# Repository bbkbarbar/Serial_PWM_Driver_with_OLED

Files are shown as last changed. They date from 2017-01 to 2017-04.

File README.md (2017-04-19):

# Serial PWM Driver with optional OLED display

##### Firmware version: 1.5
##### Hardware version: 1.45

#### Table of content:
- [Requirements](#Requirements)
  - [Used MCU](#Device)
  - [Number of output channels](#output_channels)
- [Optional feautres](#Optional_feautres)
  - [Display can be used](#Display_can_be_used)
  - [Handling further channels](#further_channels)
- [Required input line over serial communication](#Required_input_line)
- [Testing, prototyping](#testing_protoryping)
  - [Serial connection (with a Raspberry Pi Zero)](#serial_communitation_with_pi)
  - [Breadboard testing](#Breadboard_testing)
  - [Breadboard testing with all parts on output side](#Breadboard_testing_with_outputs)
- [PCB design](#PCB_design)
  - [Part list](#part_list)
  - [PCB prototype](#PCB_prototype)
  - [First prototype dry test](#prototype_dry_test)
  - [Final placing](#final_placing)
- [Measurements](#Measurements)
  - [Power consumption](#power_consumption)
  - [Memory and program storage utilization on ATmega328](#memory_useage)
- [ToDo list](#todo)
- [Changelog](#changelog)

## <a name="Requirements"> Requirements </a>

 - This device can control individual PWM outputs as "channels".

 - It get commands from any other device over serial communication.

 (e.g.: from a Raspberry Pi or a Bluetooth Serial module)

 - It need to be able to control any DC device at least with 5A power consumption per channel.

 - Need to elecrically separete output channels from MCU circuit and from connected serial device to protect own board and the attached device on the other side of serial communication
 in case of any electrial issue.
 (This will separation is that what will be named as "MCU-side" and "output-side" of this board.)
 This separation based on optocouplers.

 - More output channels need to be able to updated in same time
even if any of those channels has no new value (e.g. When it drives RGB lights and new commands contains only the red and green values)

##### <a name="Device"> Used MCU: </a>
Arduino Nano v3 [(eBay link)](http://www.ebay.com/itm/191773759569?_trksid=p2057872.m2749.l2649&ssPageName=STRK%3AMEBIDX%3AIT)

##### <a name="output_channels"> Number of output channels: </a>
6 channels with 8 bit PWM outputs - based on physical limitation of arduino board.

    Note: Can handle 12bit inputs too.
    For this function define macro:

        USE_12BIT_INPUT_VALUES

### <a name="Optional_feautres"> Optional feautres: </a>

###### <a name="Display_can_be_used"> Display can be used </a> (required library: [Arduino-SSD1306 Ascii](https://github.com/bbkbarbar/Arduino-SSD1306Ascii) ):
    Can handle simple oled display over I2C or SoftSPI protocols to show current values.
    For this feature define one of the following macros:

        USE_OLED_DISPLAY_I2C or
        USE_OLED_DISPLAY_SPI

    Important note:
        Do not define any "USE_OLED_DISPLAY..." macro (comment it out) if display is not connected.
        It will stop working when it tries to communicate with the display and there is no display.

###### <a name="further_channels"> Handling further channels </a>

    Can handle more than 6 channels (what is the physical limitation
    by number of pwm channels on Arduino Nano board)
    If this feature is in use, then it forwards the received commands for a "slave instance"
    when the channel id (of the received command) is over the range of "own channels".
    A second, SoftwareSerial bus is used for forwarding of command to the slave instance of Serial PWM driver
    For this feature define the following macro:

        HANDLE_FURTHER_CHANNELS

### <a name="Required_input_line"> Required input line over serial communication </a>

    Input line for any channel: channel_num value

    | Input mode | Using "further channels" option | channel_num | value   |
    | ---------- | ------------------------------- | ----------- | ------- |
    |    8 bit   |              No                 | 0..5        | 0.. 255 |
    |    8 bit   |              Yes                | 0..ch_max   | 0.. 255 |
    |   12 bit   |              No                 | 0..5        | 0..4095 |
    |   12 bit   |              Yes                | 0..ch_max   | 0..4095 |

    ch_max: depens on the count of devices (= 6 * device count)

    Examples: 0 255
              5 4095

## <a name="testing_protoryping"> Testing, prototyping </a>

##### <a name="serial_communitation_with_pi"> Serial connection with a Raspberry Pi Zero </a>

    Serial PWM Driver board get commands over strandard serial communication.
    In my case the other device (what sends the commands) will be a
    RaspberryPi Zero (link below).

    RaspberryPi (and many other devices) using serial communication
    with signal level of 3,3V.
    In direction of Pi -> Arduino it works fine, because arduino can read Pi's
    3,3V "high" signal as a "high" signal, since it is significantly higher
    voltage than 2,5V (what is the middle of range 0V-5V), but:
    In direction of Arduino -> Pi we have to apply a voltage divider to make
    arduino's 5V signal level lower to protect the RaspberryPi.
    For this we can use simple resistors with values of 220 and 470 Ohm,
    to create a 3,3V signal from Arduino's TX signal.

    Note: According to the measured power consumtion of
    Serial PWM Driver board on MCU side, it can be powered directly
    from VCC of RaspberryPi.
    If it needed because of any reason, Serial PWM Driver board can powered
      - from external VCC (over it's VCC connector)
      - from external raw input (6V-15V over RAW connector)
    Important:
      If Serial PWM Driver board is powered from any external source
      (what is not the same as the power source of connected serial device),
      then the VCC (5V) connection of "Serial In" MUST be interrupted
      (via the jumper on the board).

[MCU side power consumtion can be found below](#power_consumption)

[RaspberryPi Zero](https://www.raspberrypi.org/blog/raspberry-pi-zero/)

Sample connection between Serial PWM Driver and RaspberryPi:

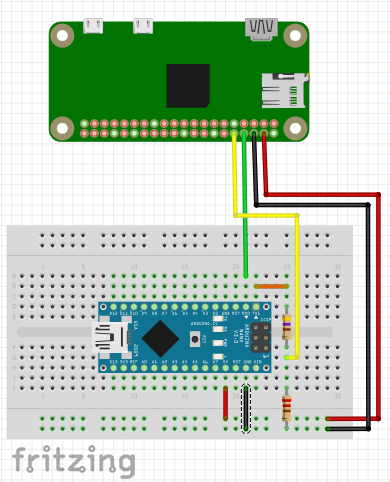
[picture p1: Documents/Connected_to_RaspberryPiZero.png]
Sample connection between Serial PWM Driver and RaspberryPi


##### <a name="Breadboard_testing"> Breadboard testing </a>

##### Testing v1.1 and v1.2 with display:
v1.1 with I2C display
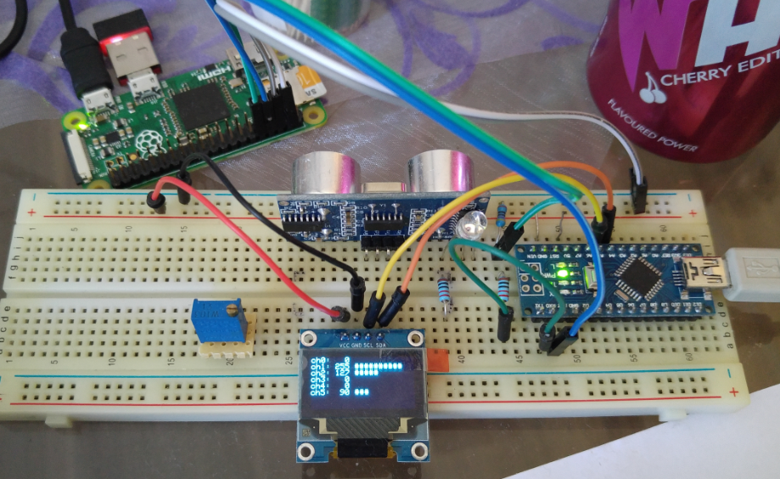
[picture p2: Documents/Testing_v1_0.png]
Testing @ v1.0 with I2C display v1.1 with I2C display

v1.2 with I2C display and sample output RGB leds
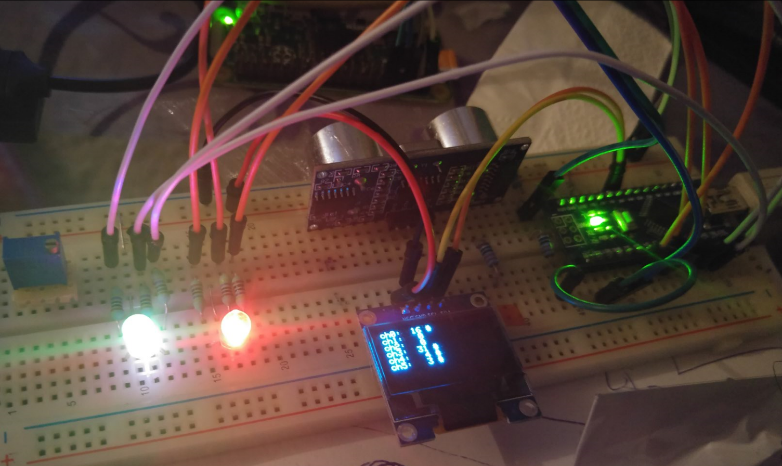
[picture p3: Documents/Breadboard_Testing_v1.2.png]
v1.2 with I2C display and sample output RGB leds


##### Testing v1.3 with 2 instances with I2C and SPI displays:

Two instances (left one is the "master device" with blue I2C display and "FURTHER_CHANNELS" feature enabled, right one with white SPI display)
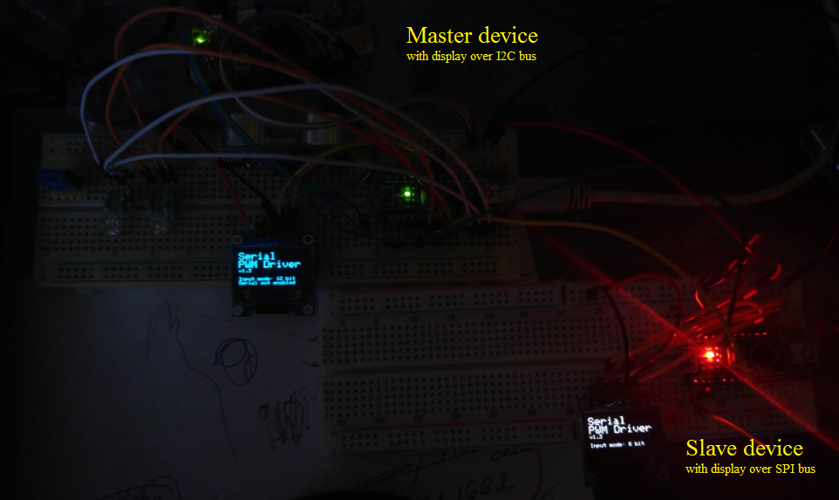
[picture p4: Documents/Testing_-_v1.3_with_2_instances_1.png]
Two instances (left one is the "master device" with blue I2C display and "FURTHER_CHANNELS" feature enabled, right one with white SPI display)


Send pwm commands from raspberryPi using the [attached python script](https://github.com/bbkbarbar/Serial_PWM_Driver_with_OLED/blob/master/Testing_with_RaspberryPi/pwm_serial_12ch.py):
Send pwm commands from raspberryPi with attached python script

Two instances after command has been received
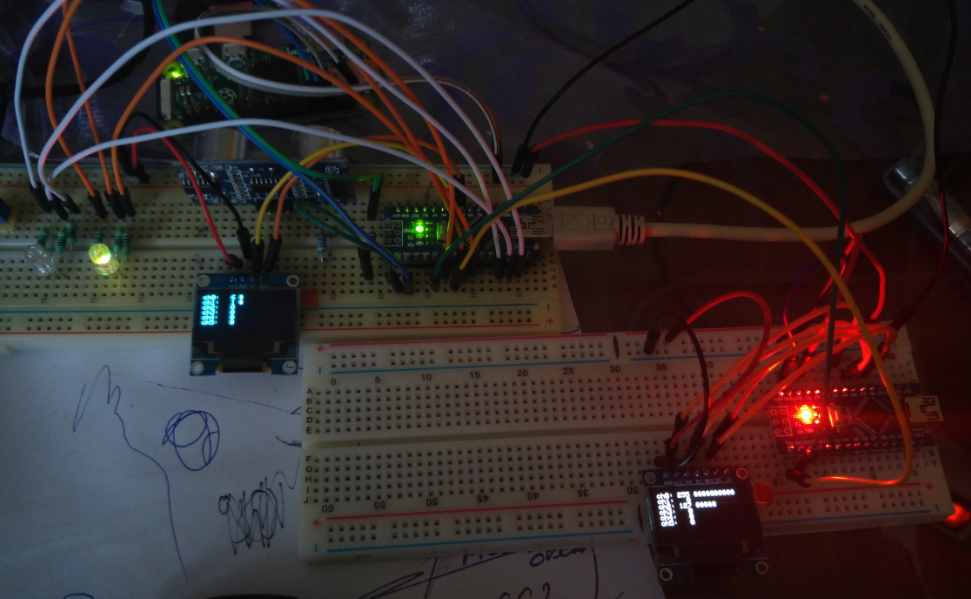
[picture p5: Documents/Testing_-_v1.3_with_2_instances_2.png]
Two instances after command has been received


##### <a name="Breadboard_testing_with_outputs"> Breadboard testing with all parts on output side </a>

    Firmware:          v1.3
    Used layout as Hw: v1.44

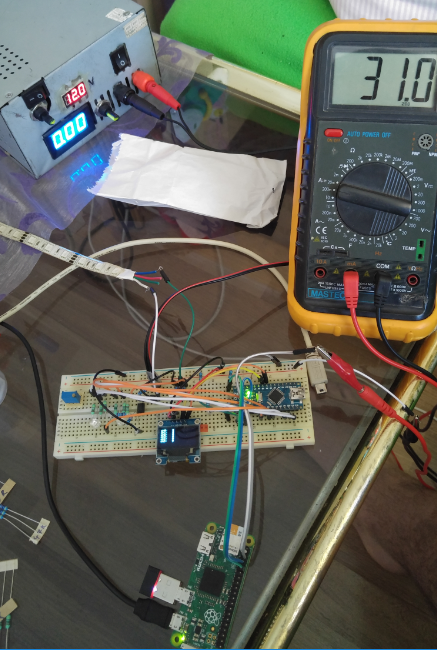
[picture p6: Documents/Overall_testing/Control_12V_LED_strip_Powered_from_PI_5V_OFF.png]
Testing with 0% output


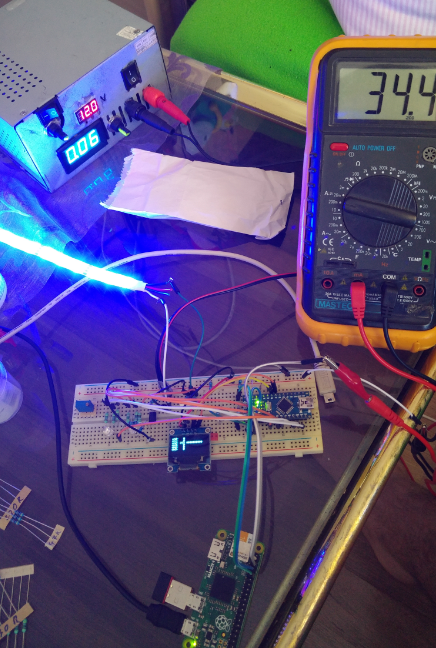
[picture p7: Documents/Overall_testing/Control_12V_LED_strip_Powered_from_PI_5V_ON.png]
Testing with 100% output


### <a name="PCB_design"> PCB design </a>
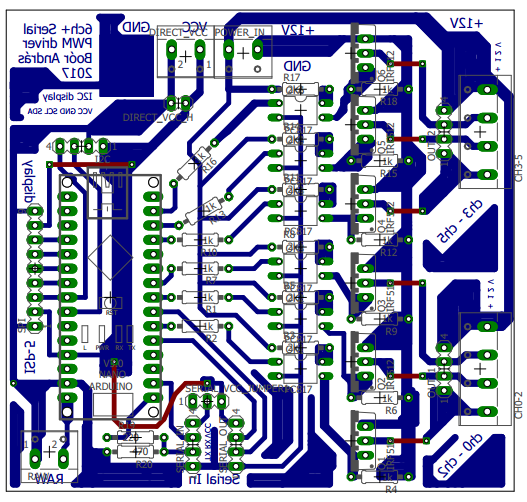
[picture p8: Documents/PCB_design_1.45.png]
PCB design v1.45


##### Eagle schamatic available as zip & pdf:
[Serial_PWM_Driver_eagle_design](https://github.com/bbkbarbar/Serial_PWM_Driver_with_OLED/blob/master/Schematic_designs/Eagle_designs/Serial_PWM_driver_-_Eagle_desing.zip)
<br>[PCB design as PDF](https://github.com/bbkbarbar/Serial_PWM_Driver_with_OLED/raw/master/Schematic_designs/Eagle_designs/PCB_design_v1.45_bottom.pdf)

##### <a name="part_list"> Part list </a> available as [HeStore](https://www.hestore.hu/) basket:
 - [Complete](https://raw.githubusercontent.com/bbkbarbar/Serial_PWM_Driver_with_OLED/master/Schematic_designs/Part%20lists/hestore_buy_list_v1.45_Complete.xml)
 - [Without arduino](https://raw.githubusercontent.com/bbkbarbar/Serial_PWM_Driver_with_OLED/master/Schematic_designs/Part%20lists/hestore_buy_list_v1.45_without_Arduino.xml)

##### <a name="PCB_prototype"> PCB prototype </a> (hw v1.45)
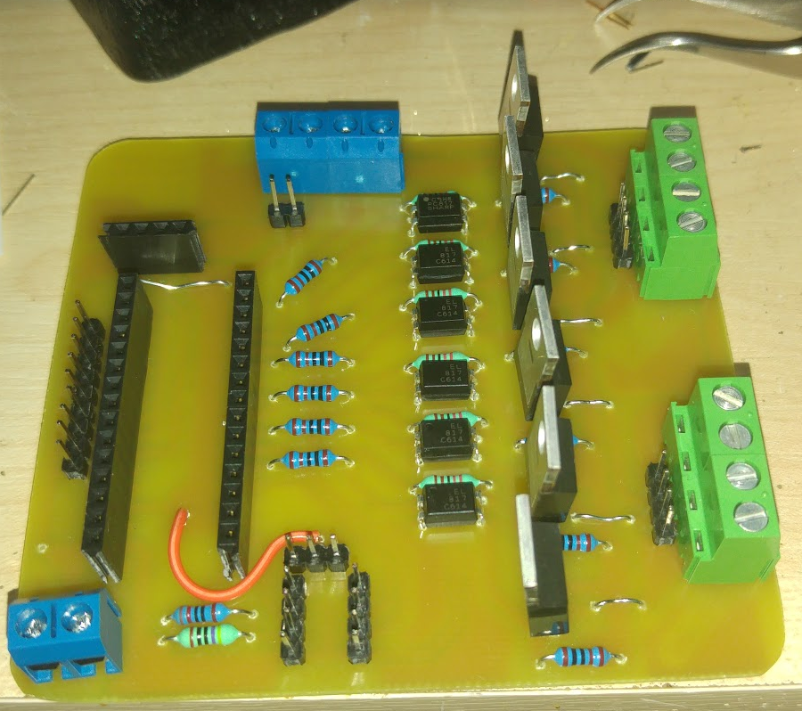
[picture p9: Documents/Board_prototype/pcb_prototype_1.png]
PCB prototype 1


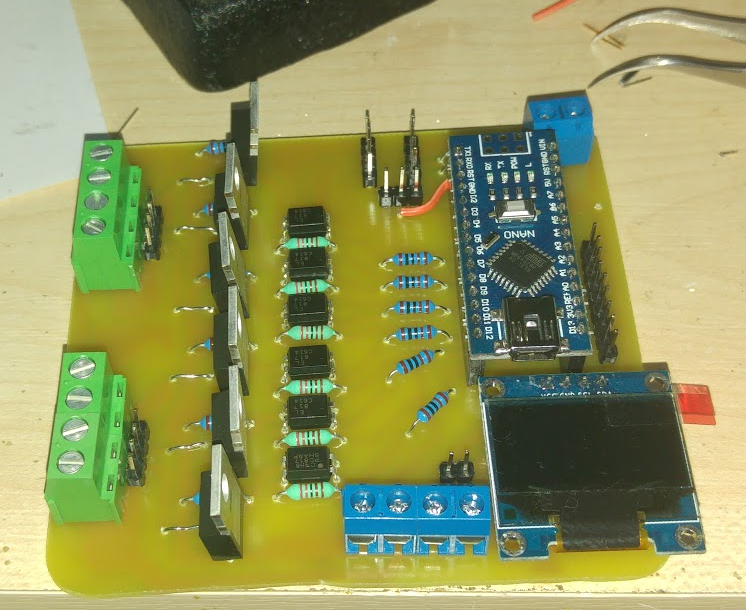
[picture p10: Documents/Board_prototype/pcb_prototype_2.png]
PCB prototype 2


##### <a name="prototype_dry_test"> First prototype dry test </a>
 - Firmware v1.3
 - Hw v1.45

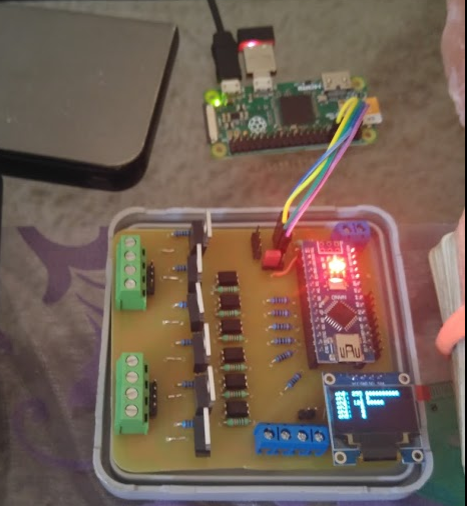
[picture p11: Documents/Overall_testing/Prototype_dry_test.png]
First prototype dry test


##### <a name="final_placing"> Final placing </a>

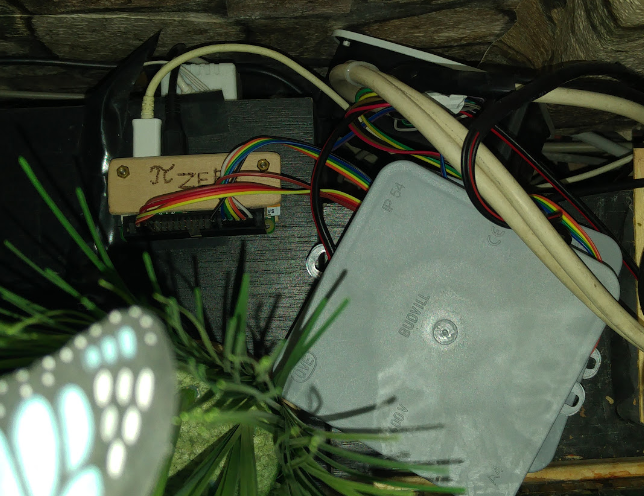
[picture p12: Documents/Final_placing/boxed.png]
Final placing


### <a name="Measurements"> Measurements </a>

##### <a name="power_consumption"> Power consumption </a>
On MCU side:

| Condition | Consumption on VCC |
| :---: | :---: |
| 0% output on all channels | 25,6 mA |
| 100% output on 1 channel | 29,0 mA |
| 100% output on 3 channels | 36,2 mA |
| 100% output on all channels | 46,8 mA (calculated) |

##### <a name="memory_useage">  Memory and program storage utilization on ATmega328 </a> (Arduino Nano v1.3):

| Option(s) used | Program storage  | Dynamic memory  | Sw version |
| :---: | :---: | :---: | :---: |
| With I2C display and using further channels | 9018 bytes (29%) | 429 bytes (20%) | v1.4 |
| Without any optional feature | 8876 bytes (28%) | 425 bytes (20%) | v1.2 |

### <a name="todo"> ToDo </a>
 - [x] Modify pinout config of softSpi display according to the pin order on display's pcb.
 - [x] Modify PCB design: Leave enaugh space between arduino and optional I2C display (when display connected directly on the board).
 - [X] Modify PCB design: Add pin-header to SoftSPI connection of optional display (it should be 2-sided (rotateable) if it's possible)
 - [X] Add termial connector for using optional 5V power supply for arduino (e.g. get VCC power directly from raspberry)
 - [X] Measure the power consumption before start using with direct 5V power supply (31mA)
 - [X] Check appropirate layout (enaugh space for connect additional boards directly)
 - [X] Create RTU PCB version
 - [X] Build first usable prototype
 - [X] Testing with real output devices
 - [X] Measure power consumption with real output devices
 - [X] Implement requirement to update RGB channels together
 - [ ] Update PCB design with missing labels (hw version, serial output)

### <a name="changelog"> Changelog </a>
    v1.5
      Store output values for recover after restart device.
      After restoring values, it will save 0 value for all channels.
      Thereby all output channel can be set for 0 with restart twice.
    v1.4
      Output channels can be linked together, to be able to update
      RGB channels together in same time
    v1.3
      Add optional feautre for handling more channels with fowarding to an other instance
    v1.2
      Add optional feautre for handling 8 and 12 bit wide input values
      (output works with 8 bit resolution in all case.)
    v1.1
      Add optional feautre for using I2C or SPI display

#### Created by:
    Andras Boor
    2017.01

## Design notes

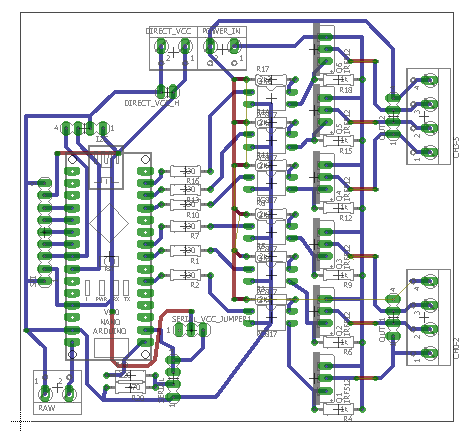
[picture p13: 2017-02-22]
Documents/PCB_design_1.42.png

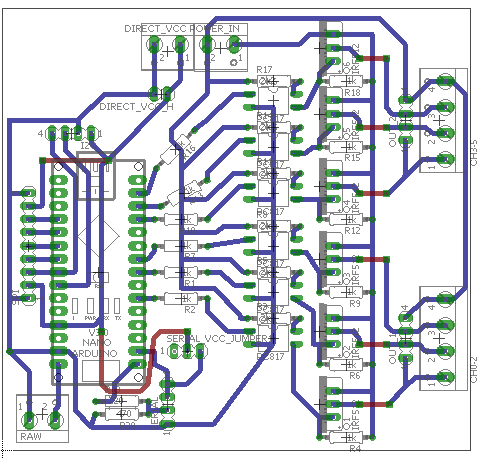
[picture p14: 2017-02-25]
Documents/PCB_design_1.44.png

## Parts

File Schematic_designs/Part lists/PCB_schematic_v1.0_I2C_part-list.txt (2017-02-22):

Partlist

Exported from PCB_schematic_v1.0.brd at 2017.01.29. 13:27

EAGLE Version 8.0.0 Copyright (c) 1988-2017 Autodesk, Inc.

Part              Value            Package    Library          
  
U1                Arduino          Nano       Arduino-clone    
OK1               PC817            DIL04      optocoupler      
OK2               PC817            DIL04      optocoupler      
OK3               PC817            DIL04      optocoupler      
OK4               PC817            DIL04      optocoupler      
OK5               PC817            DIL04      optocoupler      
OK6               PC817            DIL04      optocoupler      
Q1                IRLZ44N          TO220BV    transistor-power 
Q2                IRLZ44N          TO220BV    transistor-power 
Q3                IRLZ44N          TO220BV    transistor-power 
Q4                IRLZ44N          TO220BV    transistor-power 
Q5                IRLZ44N          TO220BV    transistor-power 
Q6                IRLZ44N          TO220BV    transistor-power 
CH0-2             Terminal-4       W237-4     con-wago-500     
CH3-5             Terminal-4       W237-4     con-wago-500     
RAW               Terminal-2       W237-132   con-wago-508      
POWER_IN          Terminal-2       W237-132   con-wago-508     
VCC_IN            Terminal-2       W237-132   con-wago-508     
VCC_IN            Pin header 1x2   MA02-1     con-lstb         
SERIAL            Pin header 1x4   MA04-1     con-lstb         
SERIAL_VCC_JUMPER Pin header 1x3   MA03-1     con-lstb         
I2C               Pin header 1x4   MA04-1     con-lstb         
OUT_1             Pin header 1x4   MA04-1     con-lstb         
OUT_2             Pin header 1x4   MA04-1     con-lstb         
R1                330              0207/10    rcl              
R2                330              0207/10    rcl              
R3                2k2              0207/10    rcl              
R4                1k               0207/10    rcl              
R5                2k2              0207/10    rcl              
R6                1k               0207/10    rcl              
R7                330              0207/10    rcl              
R8                2k2              0207/10    rcl              
R9                1k               0207/10    rcl              
R10               330              0207/10    rcl              
R11               2k2              0207/10    rcl              
R12               1k               0207/10    rcl              
R13               330              0207/10    rcl              
R14               2k2              0207/10    rcl              
R15               1k               0207/10    rcl              
R16               330              0207/10    rcl              
R17               2k2              0207/10    rcl              
R18               1k               0207/10    rcl              
R19               220              0207/10    rcl              
R20               470              0207/10    rcl

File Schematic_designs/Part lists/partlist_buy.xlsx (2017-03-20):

Part | Package | Value | Device | Amount
CH0-2, CH3-5 | con-wago-500 | 4 | W237-4 | 2
RAW, DIRECT_VCC, POWER_IN | con-wago-500 | 2 | W237-102 | 3 | X
OK1 - OK6 | optocoupler | PC817 | DIL04 | 6 | X
Q1 - Q6 | transistor-power | IRLZ44N | TO220BV | 6
R1, R2, R4, R6, R7, R9, R10, R12, R13, R15, R16, R18 | R | 1k | 0207/10 | 18
R3, R5, R8, R11, R14, R17 | R | 2k2 | 0207/10 | 6
R19 | R | 220R | 0207/10 | 1
R20 | R | 470R | 0207/10 | 1
DIRECT_VCC_H | pin-header | 2 | MA02-1 | 1 | X
SERIAL_VCC_JUMPER1 | pin-header | 3 | MA03-1 | 1 | X
SERIAL_IN, SERIAL_OUT, OUT_1, OUT_2, I2C | pin-header | 4 | MA04-1 | 5 | X
SPI | pin-header | 9 | MA09-1 | 1 | X
U1_place | pin-header female | 15 | FA15-1 | 2 | X
U1 | Arduino Nano |  | Nano v3 | 1 | X
PCB | 9,0 * 8,5 cm | 1 | 1-side | 1
Drill | 0,8 mm | 0.8 |  | 1-2
Drill | 1,2 mm | 1.2 |  | 1

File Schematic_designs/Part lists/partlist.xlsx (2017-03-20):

Part | Package | Value | Type | Device | Amount
CH0-2, CH3-5 | con-wago-500 | 4 | W237-4 | W237-4 | 2
RAW, DIRECT_VCC, POWER_IN | con-wago-500 | 2 | W237-102 | W237-102 | 3
OK1 - OK6 | optocoupler | PC817 |  | DIL04 | 6
Q1 - Q6 | transistor-power | IRLZ44N |  | TO220BV | 6
R1, R2, R4, R6, R7, R9, R10, R12, R13, R15, R16, R18 | R | 1k | R-EU_0207/10 | 0207/10 | 18
R3, R5, R8, R11, R14, R17 | R | 2k2 | R-EU_0207/10 | 0207/10 | 6
R19 | R | 220R | R-EU_0207/10 | 0207/10 | 1
R20 | R | 470R | R-EU_0207/10 | 0207/10 | 1
DIRECT_VCC_H | pin-header | 2 |  | MA02-1 | 1
SERIAL_VCC_JUMPER1 | pin-header | 3 |  | MA03-1 | 1
SERIAL_IN, SERIAL_OUT, OUT_1, OUT_2, I2C | pin-header | 4 |  | MA04-1 | 5
SPI | pin-header | 9 |  | MA09-1 | 1
U1_place | pin-header female | 15 |  | FA15-1 | 2
U1 | Arduino Nano |  |  | Nano v3 | 1

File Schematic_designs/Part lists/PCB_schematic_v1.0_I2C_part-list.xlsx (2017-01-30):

Partlist - Exported from PCB_schematic_v1.0.brd at 2017.01.29. 13:27
Part | Value | Package | Library
U1 | Arduino Nano | Nano | Arduino-clone
OK1 | PC817 | DIL04 | optocoupler
OK2 | PC817 | DIL04 | optocoupler
OK3 | PC817 | DIL04 | optocoupler
OK4 | PC817 | DIL04 | optocoupler
OK5 | PC817 | DIL04 | optocoupler
OK6 | PC817 | DIL04 | optocoupler
Q1 | IRLZ44N | TO220BV | transistor-power
Q2 | IRLZ44N | TO220BV | transistor-power
Q3 | IRLZ44N | TO220BV | transistor-power
Q4 | IRLZ44N | TO220BV | transistor-power
Q5 | IRLZ44N | TO220BV | transistor-power
Q6 | IRLZ44N | TO220BV | transistor-power
SERIAL | Pin header 1x4 | MA04-1 | con-lstb
SERIAL_VCC_JUMPER | Pin header 1x3 | MA03-1 | con-lstb
CH0-2 | Terminal-4 | W237-4 | con-wago-500
CH3-5 | Terminal-4 | W237-4 | con-wago-500
RAW | Terminal-2 | W237-102 | con-wago-500
POWER_IN | Terminal-2 | W237-132 | con-wago-508
I2C | Pin header 1x4 | MA04-1 | con-lstb
OUT_1 | Pin header 1x4 | MA04-1 | con-lstb
OUT_2 | Pin header 1x4 | MA04-1 | con-lstb
R1, R2, R7, R10, R13, R16 | 330 | 0207/10 | rcl
R3, R5, R8, R11, R14, R17, | 2k2 | 0207/10 | rcl
R4, R6, R9, R12, R15, R18 | 1k | 0207/10 | rcl
R19 | 220 | 0207/10 | rcl
R20 | 470 | 0207/10 | rcl

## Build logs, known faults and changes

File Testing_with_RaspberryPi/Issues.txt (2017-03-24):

Python based serial output does not works with following error message:

pi@dev-pi:~ $ sudo python /home/pi/python/live/pwm_serial_6ch.py -r 100 -g 600
Traceback (most recent call last):
  File "/home/pi/python/live/pwm_serial_6ch.py", line 6, in <module>
    import serial
  File "/usr/lib/python2.7/dist-packages/serial/__init__.py", line 21, in <module>
    from serial.serialposix import *
  File "/usr/lib/python2.7/dist-packages/serial/serialposix.py", line 600, in <module>
    class Serial(PosixSerial, io.RawIOBase):
AttributeError: 'module' object has no attribute 'RawIOBase'

https://www.raspberrypi.org/forums/viewtopic.php?f=32&t=76028

Source of problem:
  In directory "/home/pi/python/live/" there were an other file with name "io.py"
  This had been used as an "overwrite" of the default io.py lib.

Solution:
  Rename that "io.py" file.
	http://stackoverflow.com/questions/23572003/why-io-module-object-has-no-attribute-rawiobase-eventhough-i-am-using-python-2

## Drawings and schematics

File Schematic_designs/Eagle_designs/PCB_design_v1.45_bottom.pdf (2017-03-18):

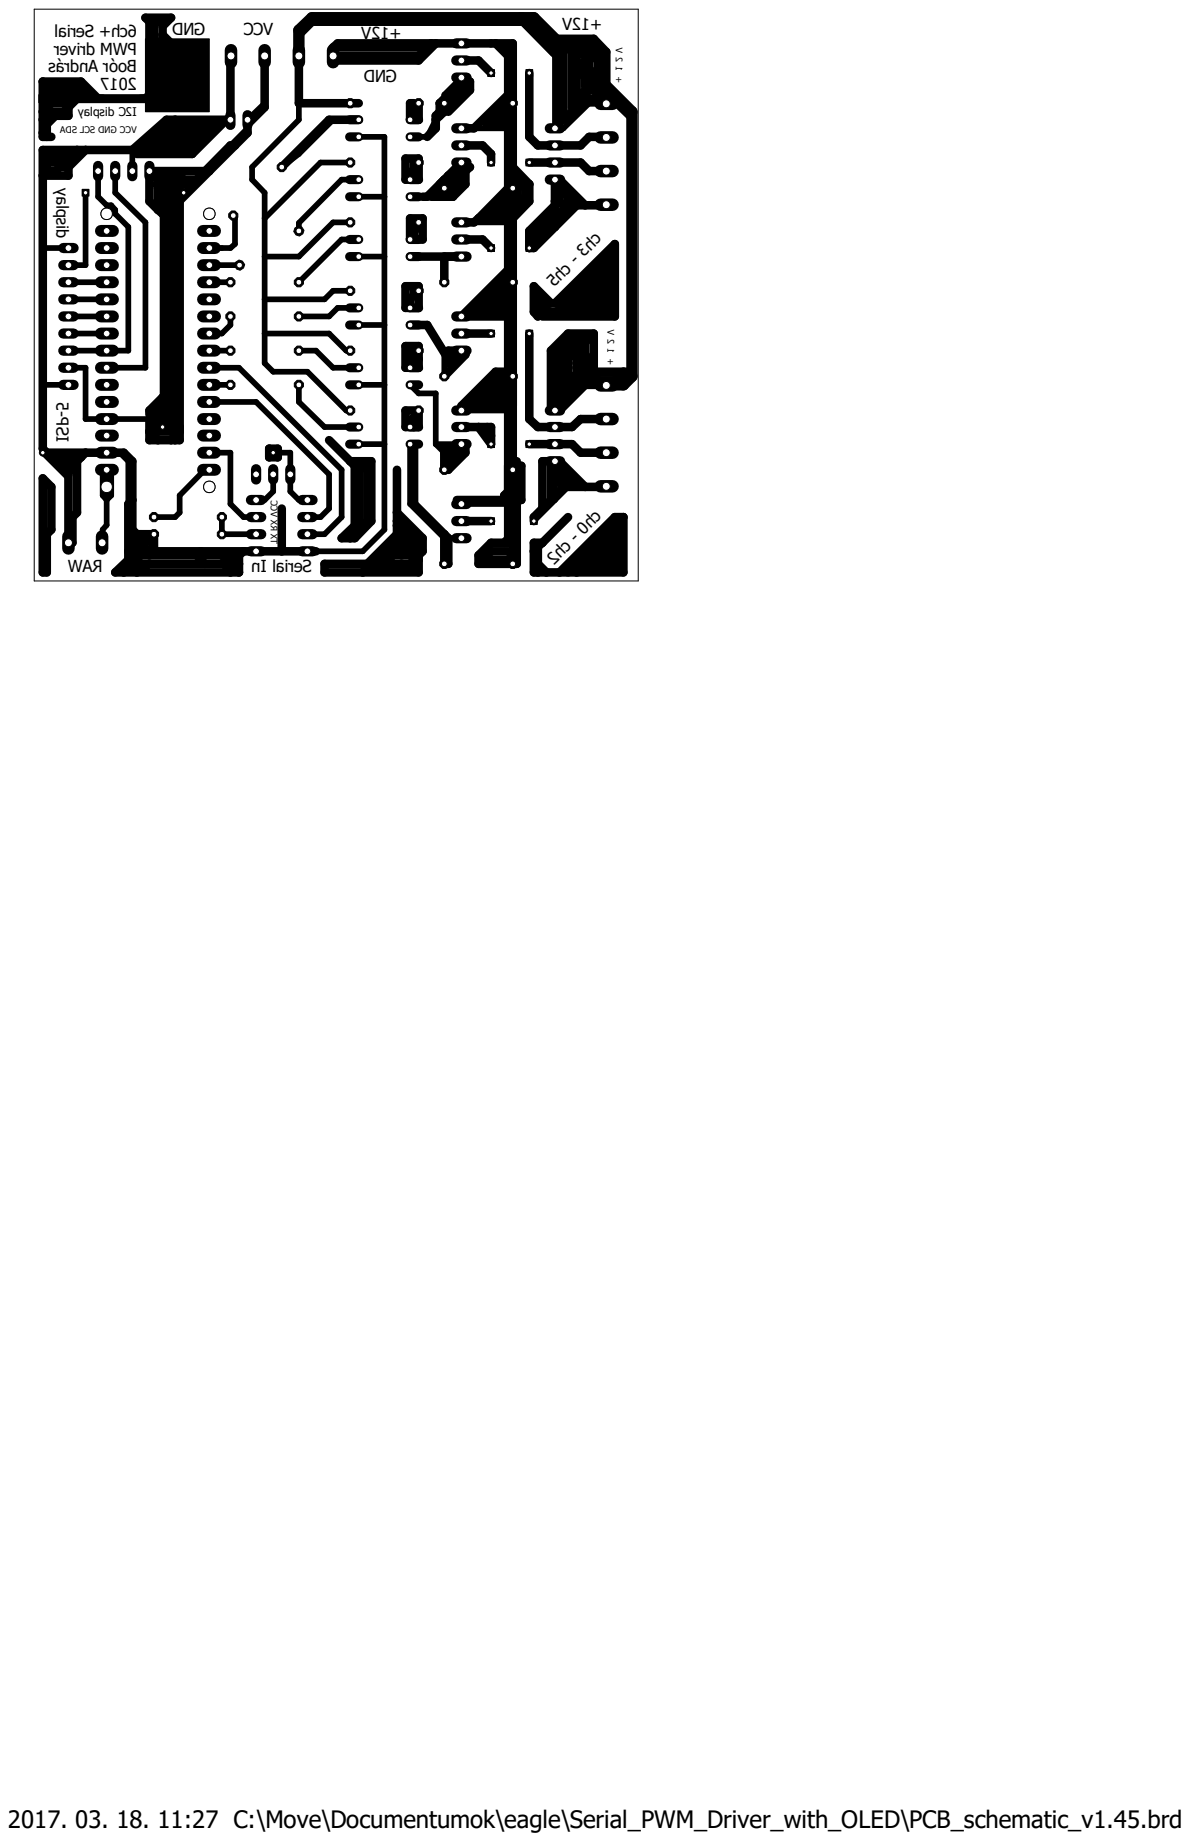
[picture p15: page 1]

2017. 03. 18. 11:27 C:\Move\Documentumok\eagle\Serial_PWM_Driver_with_OLED\PCB_schematic_v1.45.brd

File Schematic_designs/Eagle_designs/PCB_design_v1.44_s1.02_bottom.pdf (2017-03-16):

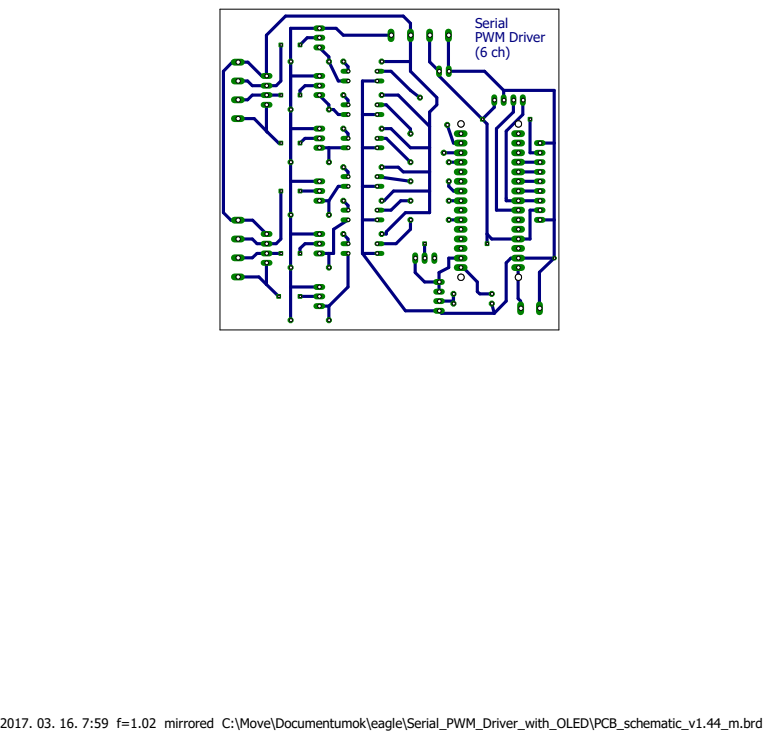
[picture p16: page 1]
Serial PWM Driver (6 ch)

2017. 03. 16. 7:59 f=1.02 mirrored C:\Move\Documentumok\eagle\Serial_PWM_Driver_with_OLED\PCB_schematic_v1.44_m.brd

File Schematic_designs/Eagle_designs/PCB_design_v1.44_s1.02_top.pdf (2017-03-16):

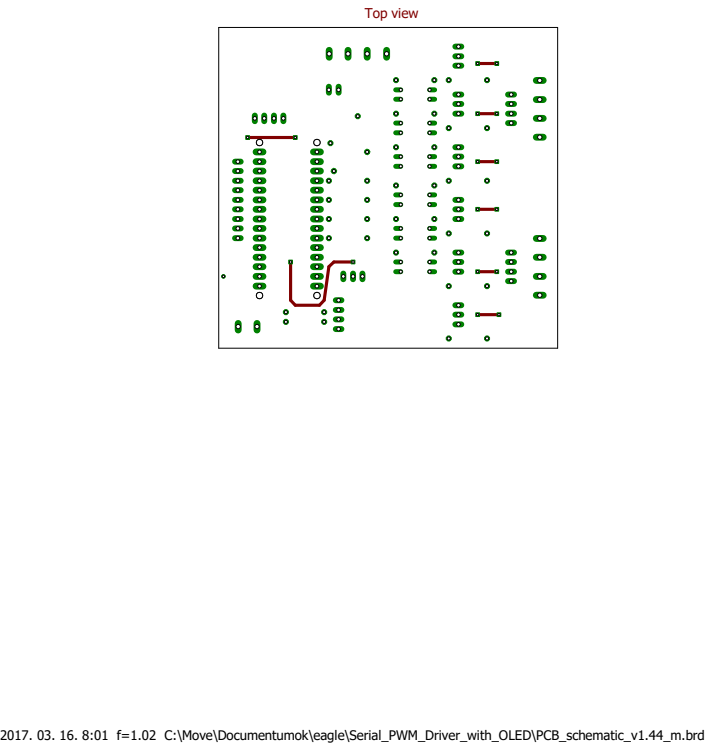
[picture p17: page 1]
Top view

2017. 03. 16. 8:01 f=1.02 C:\Move\Documentumok\eagle\Serial_PWM_Driver_with_OLED\PCB_schematic_v1.44_m.brd

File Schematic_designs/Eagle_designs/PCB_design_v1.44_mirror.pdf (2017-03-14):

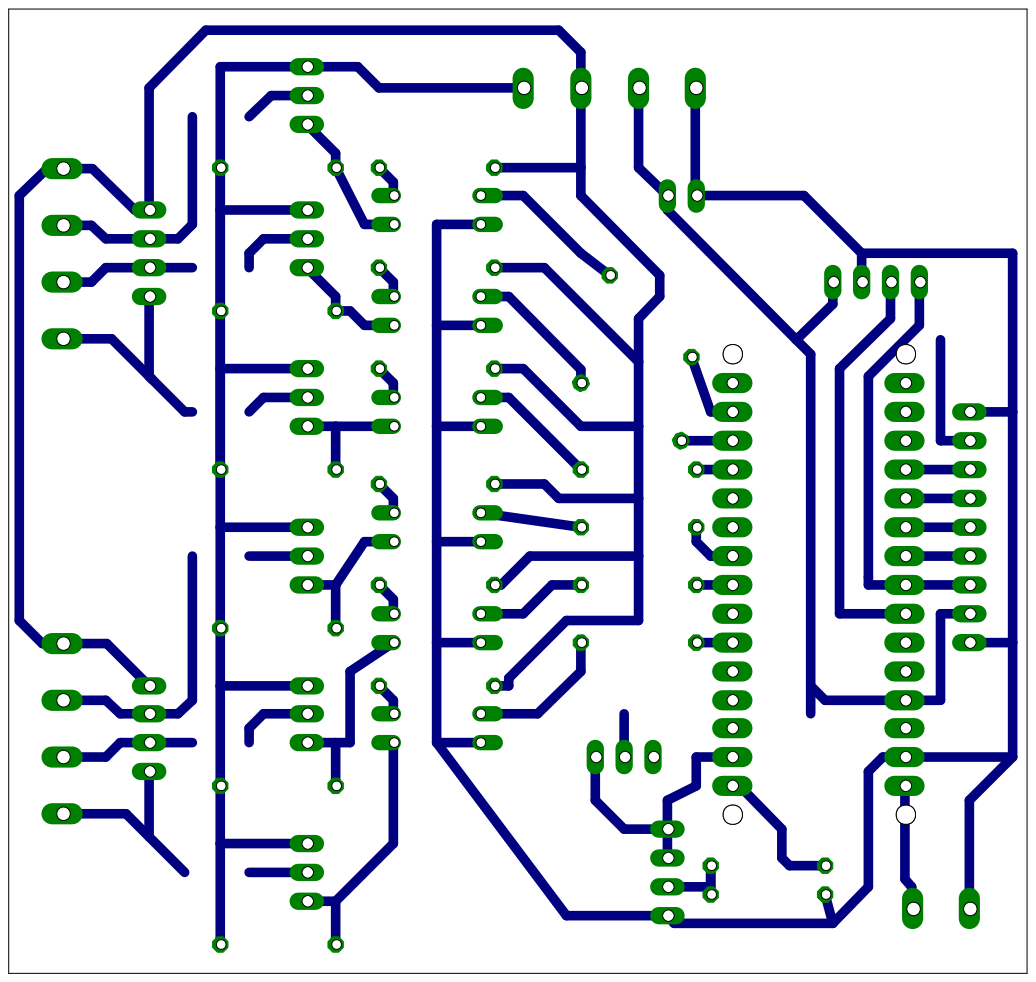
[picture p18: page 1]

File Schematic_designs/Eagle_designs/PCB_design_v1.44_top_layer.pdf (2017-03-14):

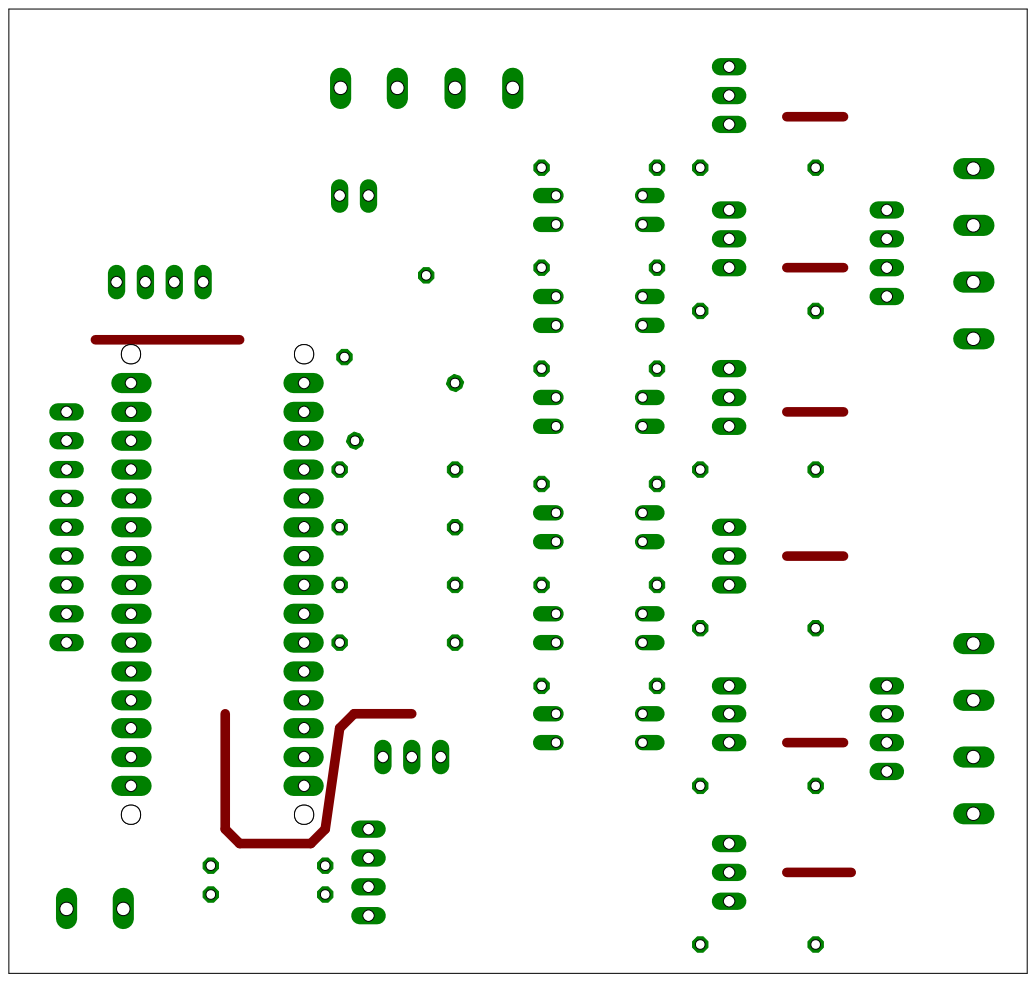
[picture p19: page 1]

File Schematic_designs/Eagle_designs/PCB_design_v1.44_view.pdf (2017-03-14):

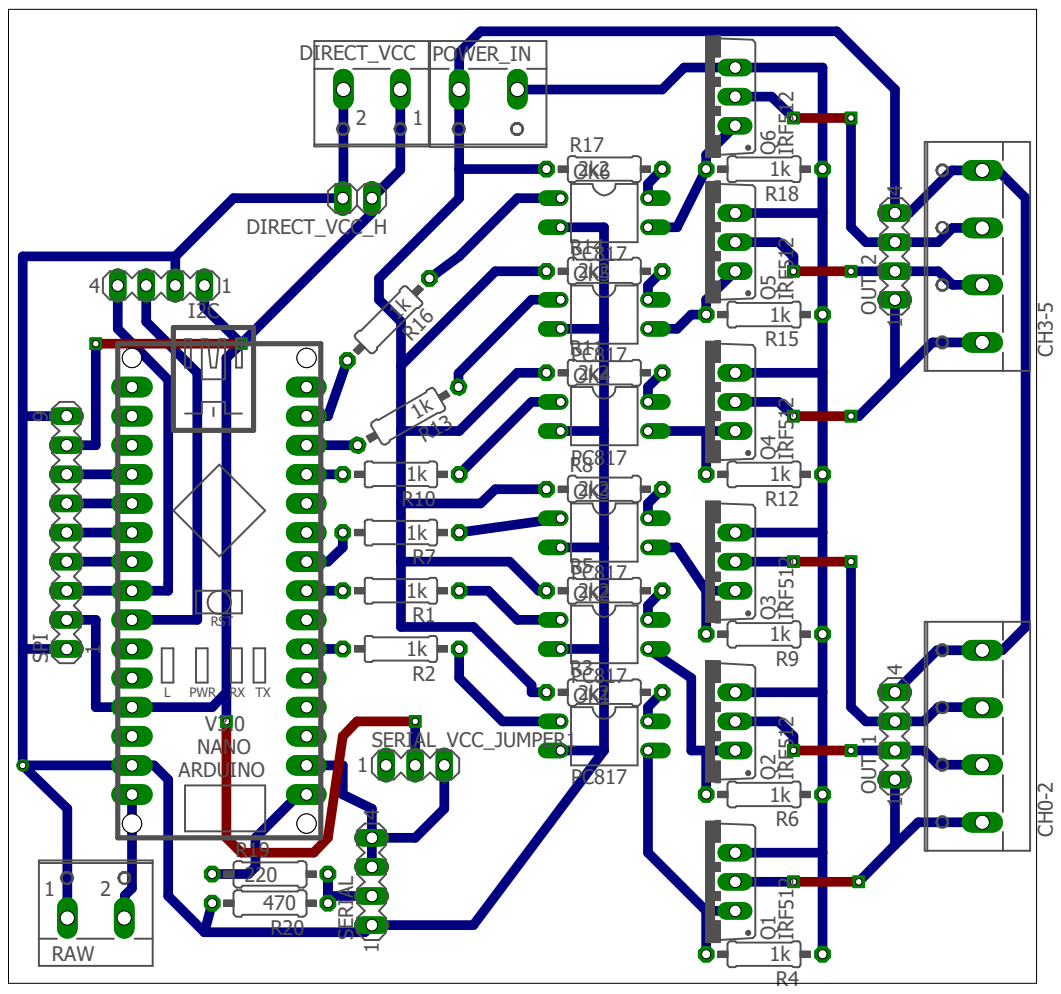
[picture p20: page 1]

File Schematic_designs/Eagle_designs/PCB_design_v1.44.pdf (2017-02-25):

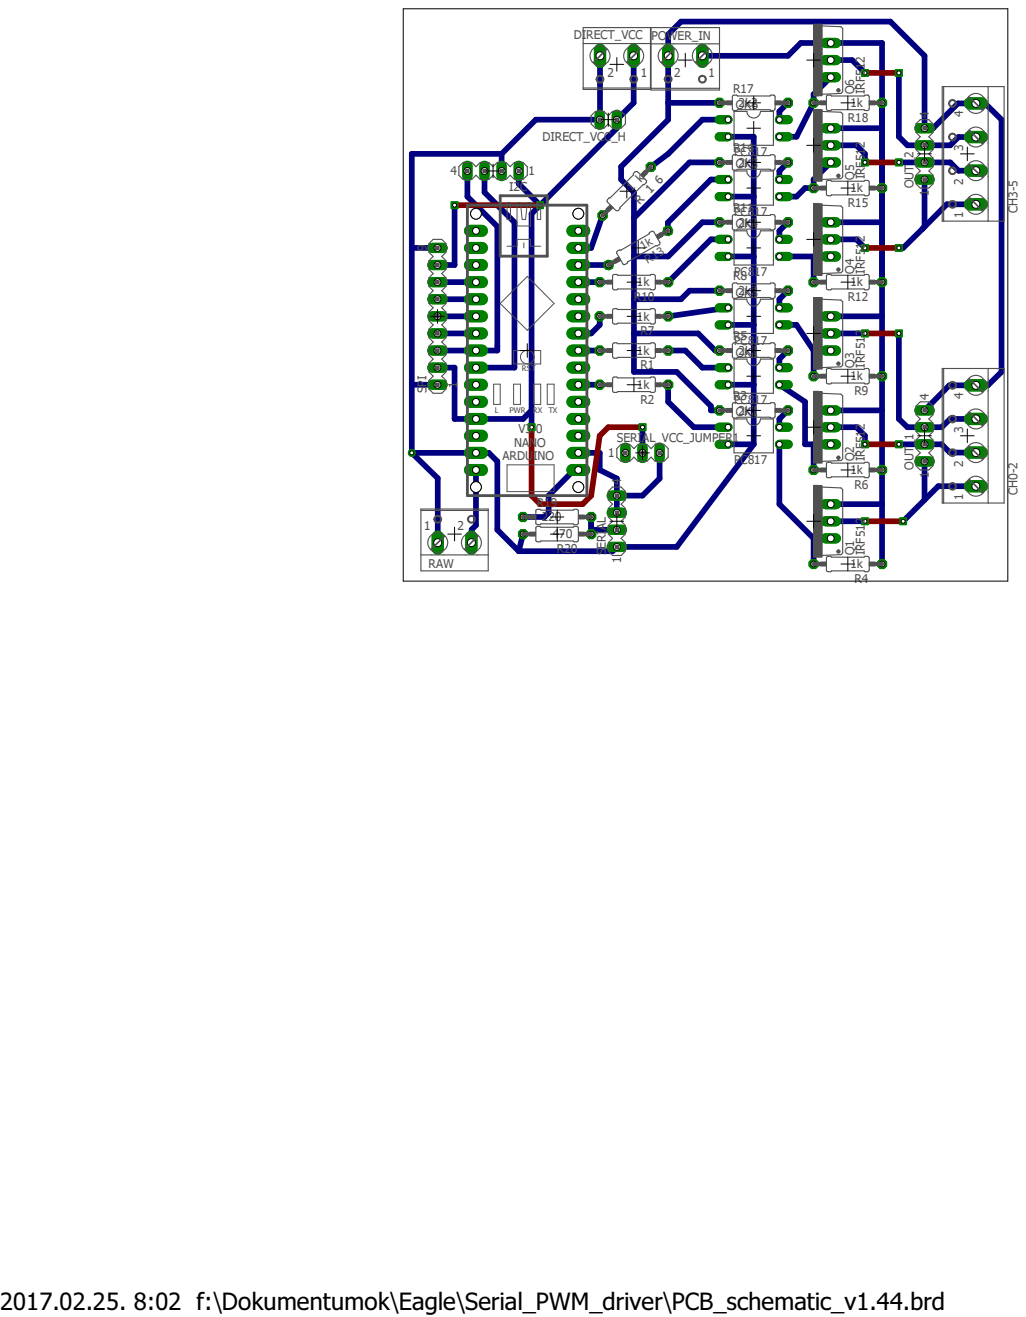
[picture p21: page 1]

R19
220
470

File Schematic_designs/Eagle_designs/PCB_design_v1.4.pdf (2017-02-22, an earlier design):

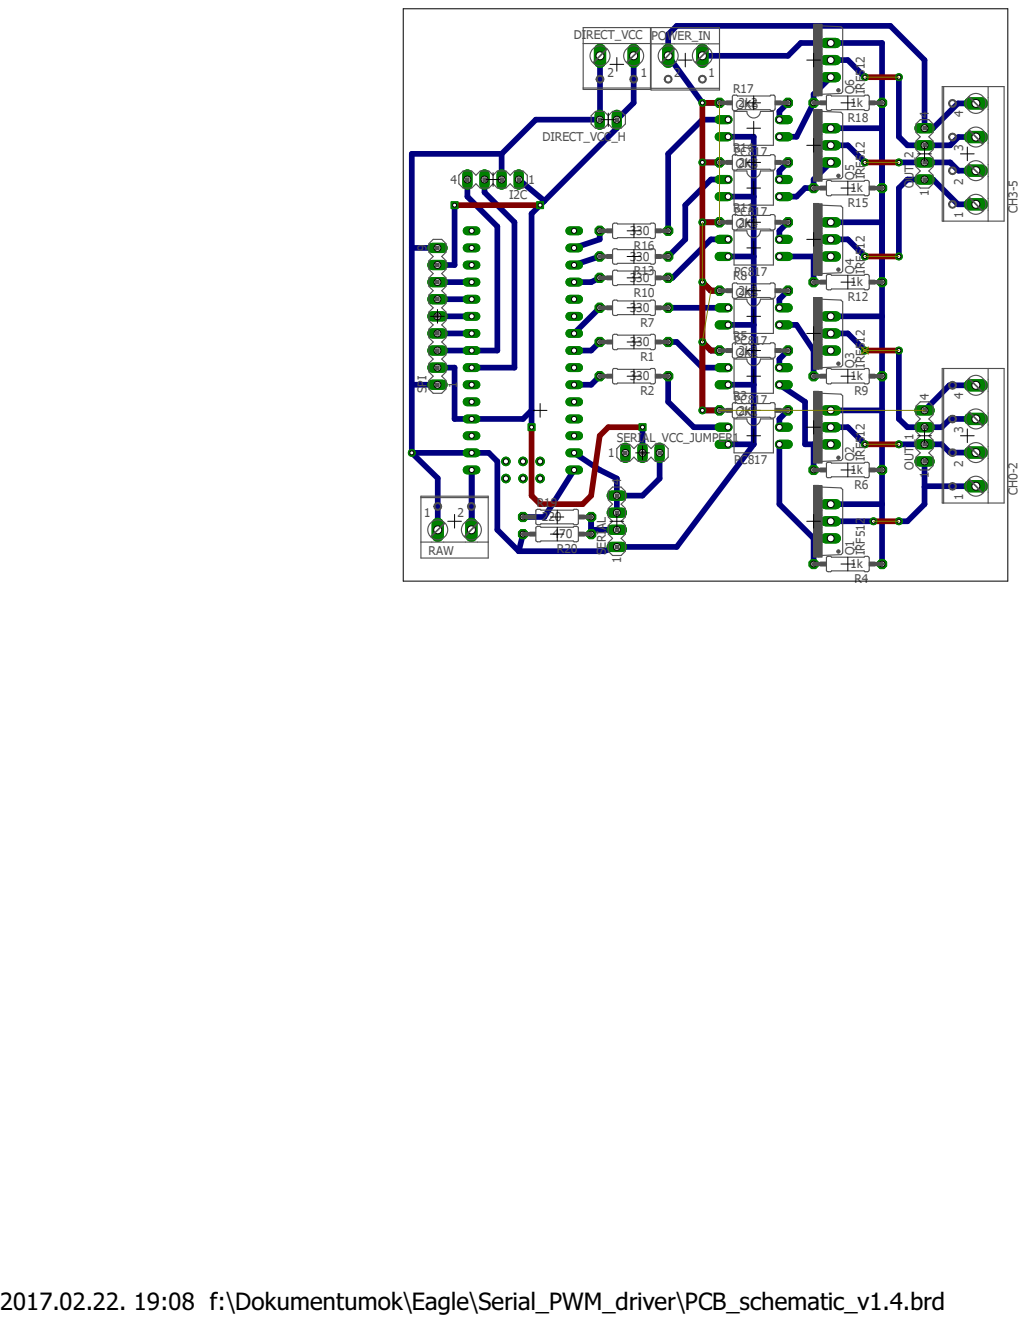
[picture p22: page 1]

2k2
OK1

220
470

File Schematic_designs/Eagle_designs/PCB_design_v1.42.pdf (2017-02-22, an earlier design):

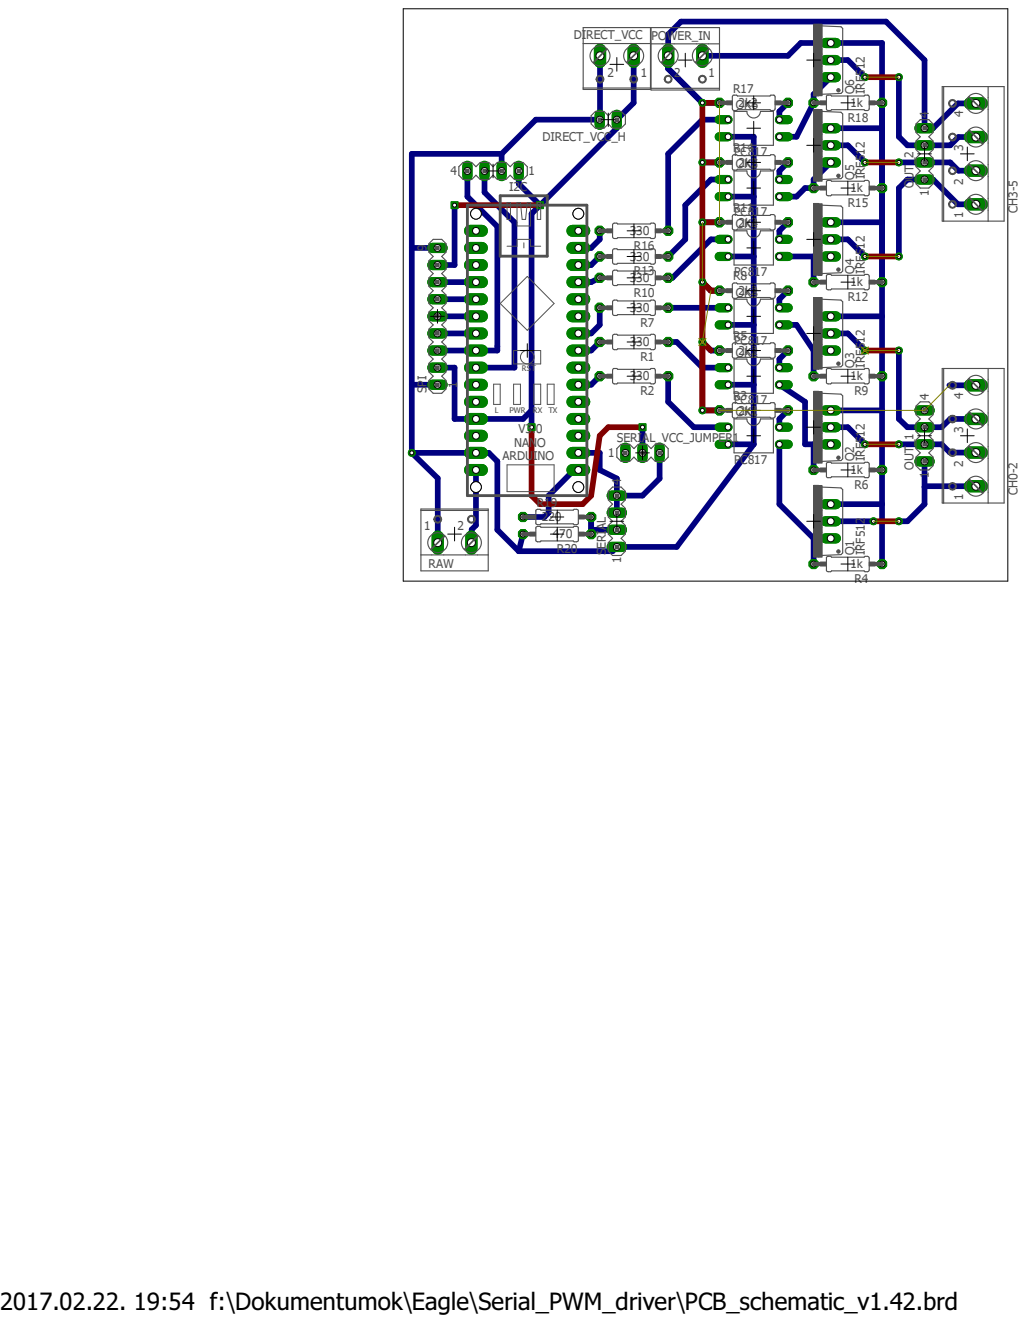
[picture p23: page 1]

2k2
OK1

R19
220
470

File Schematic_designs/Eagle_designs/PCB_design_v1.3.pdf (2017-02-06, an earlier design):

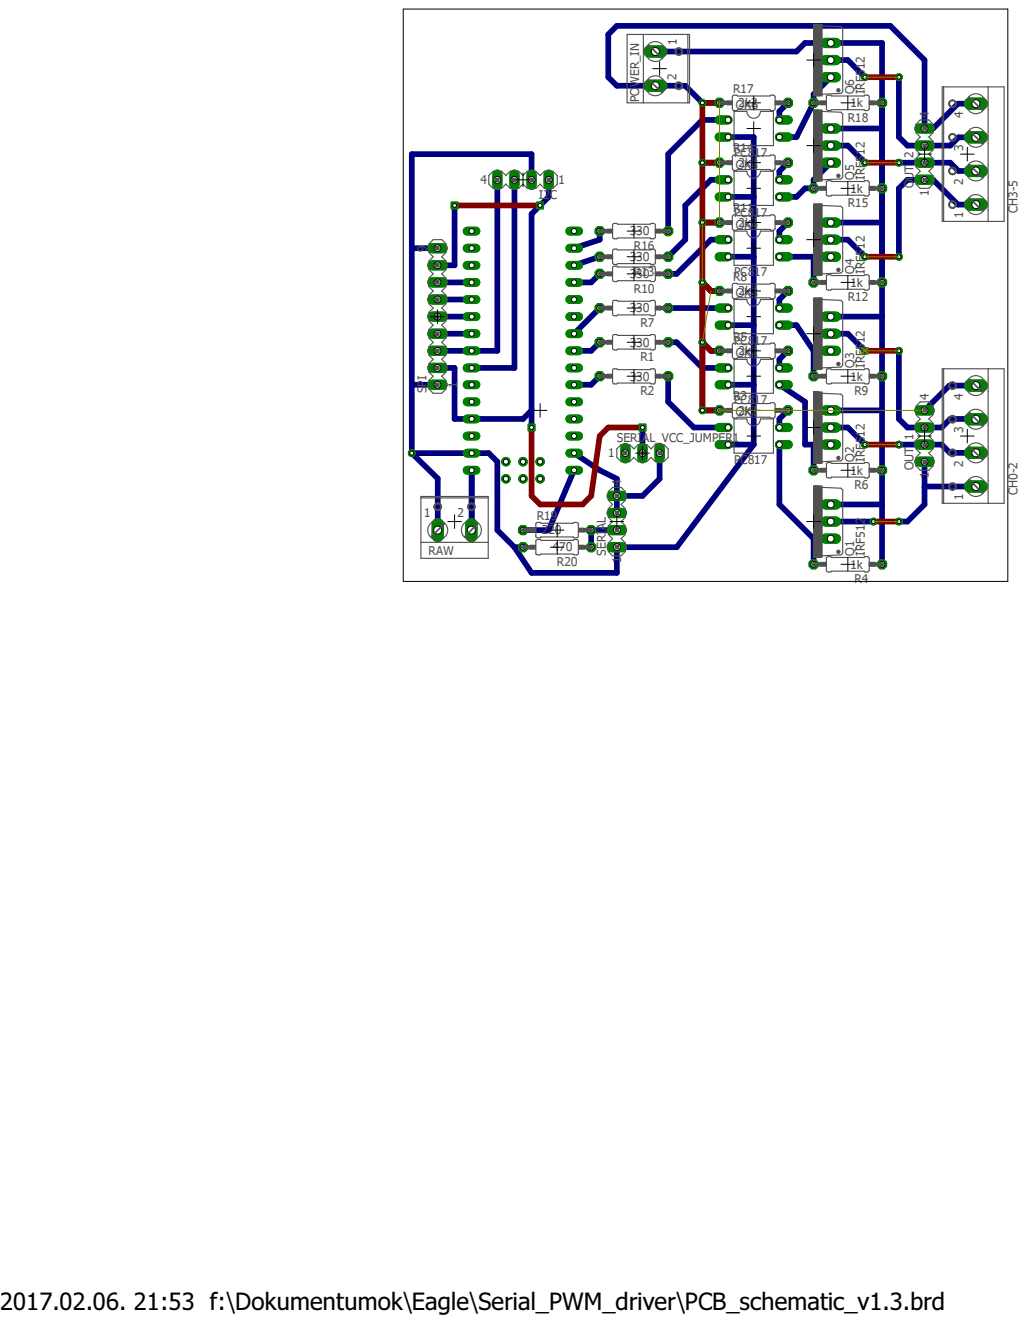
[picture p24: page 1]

2k2
OK1

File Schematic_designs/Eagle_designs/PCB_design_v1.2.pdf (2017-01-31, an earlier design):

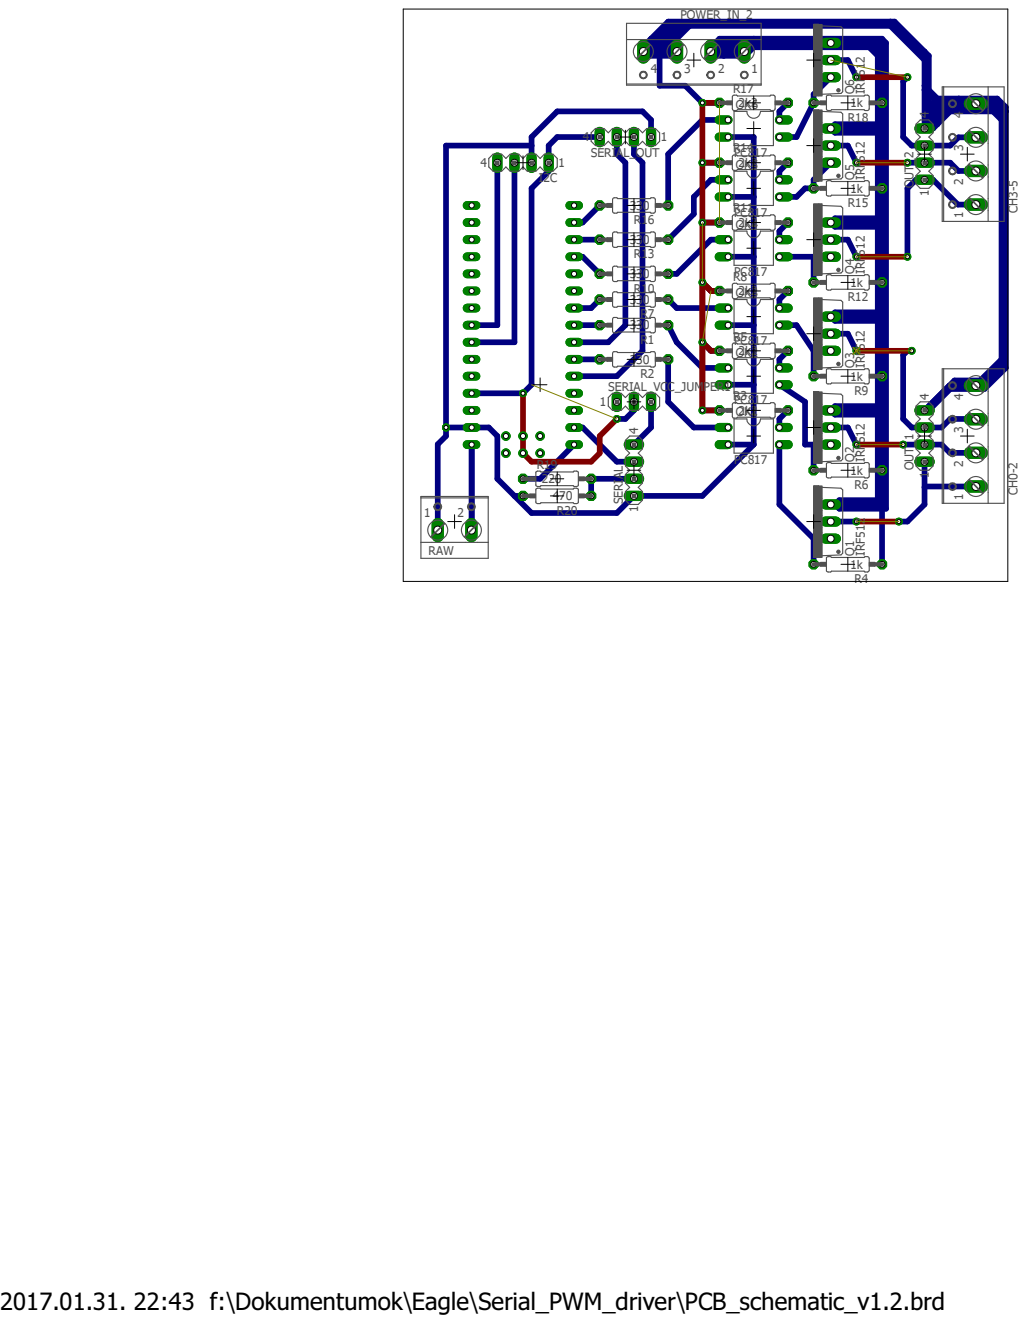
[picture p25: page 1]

220
470

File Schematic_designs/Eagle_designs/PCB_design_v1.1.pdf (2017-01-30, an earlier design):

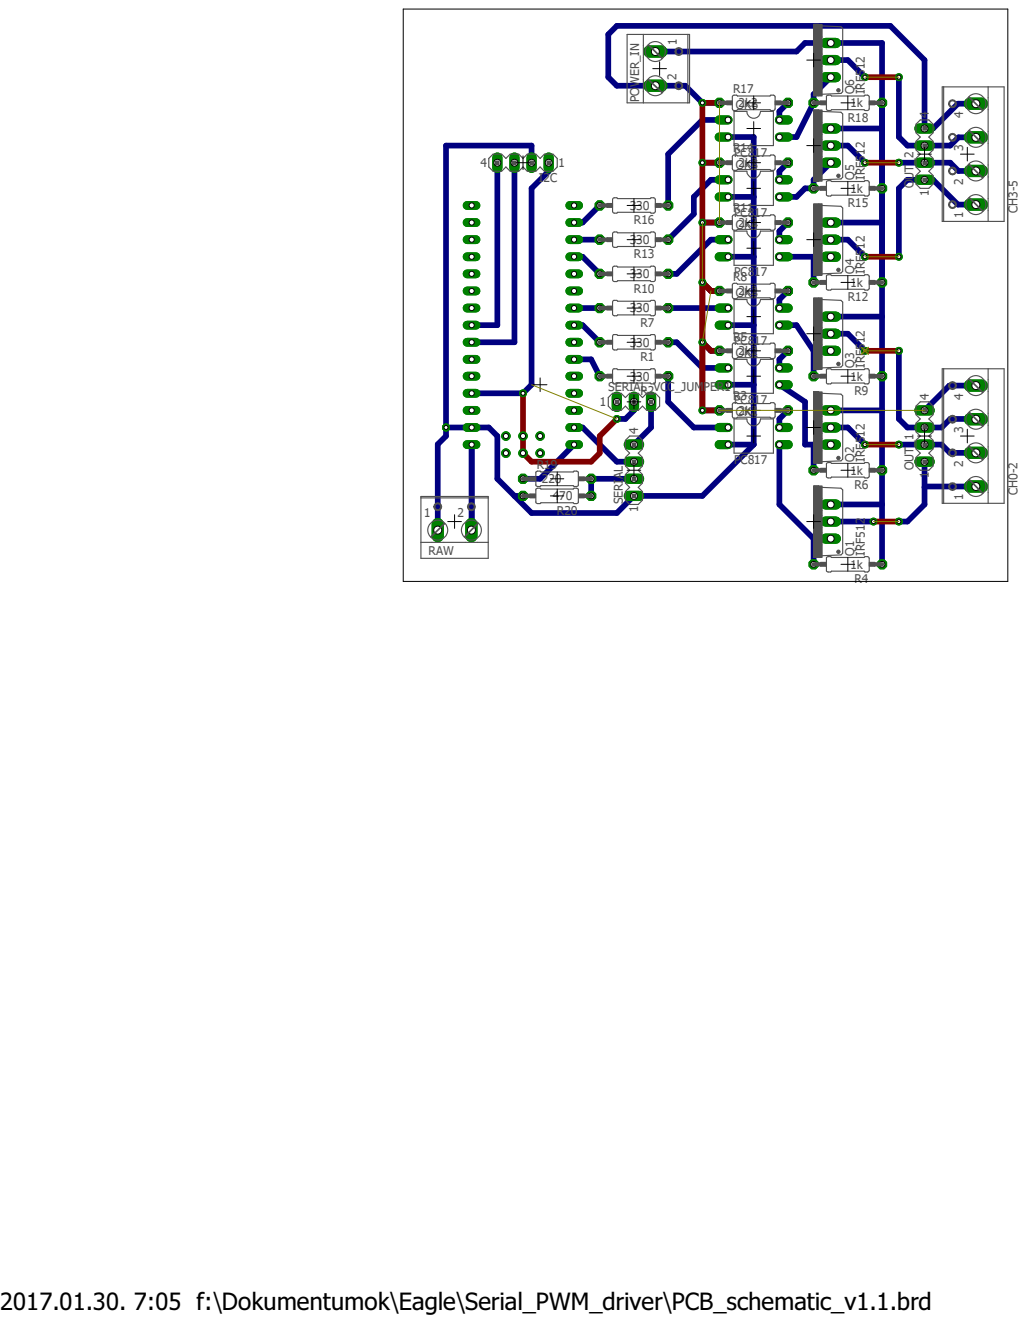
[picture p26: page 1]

2k2
OK1

220
470

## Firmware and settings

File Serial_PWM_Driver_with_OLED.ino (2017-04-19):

/*
 * Serial PWM driver
 * version 1.5
 * 
 * Device: 
 *     Arduino Nano
 * Number of output channels: 
 *     6 (8bit pwm outputs)
 *
 * Required input line over serial communication:
 * "<channel_num> <value>"
 * Where:
 *     <channel_num> is an integer in range [0..5]
 *     <value> is an integer for pwm value
 *     
 * Input value can be a 8bit pwm value or 12bit pwmvalue.
 * Note: For handle 12bit pwm inputs define the following macro:
 *       USE_12BIT_INPUT_VALUES
 *
 *
 * Optional feature:
 *  -  Display:
 *     Can handle simple oled display for show current values over I2C or SoftSPI
 *     For this feature define one of following macros: 
 *           USE_OLED_DISPLAY_I2C or 
 *           USE_OLED_DISPLAY_SPI
 *     Note: In case of using SPI display, need to define proper values for the following macros:
 *           OLED_DC, OLED_CS, OLED_D0, OLED_D1, OLED_RST
 *           In case of using I2C display, need to define proper value 
 *           for "I2C_ADDRESS_OF_DISPLAY" macro.
 * 
 *  -  Further channels:
 *     Can handle more channel than 6 (what is the physical limitation by number of arduino's pwm channels)
 *     If this feature is in use, then it forwards the received commands for a "slave instance" when 
 *     the channel id (of the received command) is over the range of "own channels".
 *     A second, SoftwareSerial bus is used for forwarding of command to the slace instance of Serial PWM driver
 *     For this feature define the following macro: 
 *           HANDLE_FURTHER_CHANNELS
 * 
 * 
 * Created by: Andras Boor
 * 2017.01.
 */
#define VERSION  "v1.5"


/*
 *  Macro definitions for optional features
 */
//#define USE_OLED_DISPLAY_I2C

#define USE_12BIT_INPUT_VALUES

#define HANDLE_FURTHER_CHANNELS

#include <EEPROM.h>


//===============================================================================================


/*
 *  Oprional feature: Handle further channels (pass command for an other instance)
 */
#ifdef HANDLE_FURTHER_CHANNELS

  #include <SoftwareSerial.h>

  // Define witch pins will be used for softSerial output bus for pass commands of further channels (channelId >= 6)
  #define SOFTSERIAL_TX              2
  #define SOFTSERIAL_RX              4
  
  SoftwareSerial serialOutput(SOFTSERIAL_RX, SOFTSERIAL_TX); // RX, TX

  /*
   *  Serial input bus for receive commands
   */
  #define SERIAL_OUTPUT_BAUNDRATE 9600

#endif



/*
 *  Serial input bus for receive commands
 */
#define SERIAL_INPUT_BAUNDRATE    9600



/*
 *  Oprional feature: Handle OLED display over I2C or SoftSPI protocols
 */

#if defined(USE_OLED_DISPLAY_I2C) || defined(USE_OLED_DISPLAY_SPI)
  #include "SSD1306Ascii.h"
#endif


#ifdef USE_OLED_DISPLAY_I2C
  #include "SSD1306AsciiAvrI2c.h"
  
  #define I2C_ADDRESS_OF_DISPLAY  0x3C  // 0X3C+SA0 - 0x3C or 0x3D
  
  SSD1306AsciiAvrI2c oled;
#endif


#ifdef USE_OLED_DISPLAY_SPI
  #include "SSD1306AsciiSoftSpi.h"

  // pin definitions for using SPI oled display over softSpi
  #define OLED_D0                   18    // A4
  #define OLED_D1                   17    // A3
  #define OLED_RST                  16    // A2
  #define OLED_DC                   15    // A1
  #define OLED_CS                   14    // A0

  SSD1306AsciiSoftSpi oled;
#endif


/*
 *  Definitions for basic functionality
 */

#define outout_channel_of_red        1
#define outout_channel_of_green      0
#define outout_channel_of_blue       2

#define PWM_OUTPUT_CH0               3
#define PWM_OUTPUT_CH1               5
#define PWM_OUTPUT_CH2               6
#define PWM_OUTPUT_CH3               9
#define PWM_OUTPUT_CH4              10
#define PWM_OUTPUT_CH5              11


#define DEFAULT_OUTPUT_VALUE         0  // can set any value in range [0..255] depending on planned useage

#define PWM_CHANNEL_COUNT            6  // based on the physical limitations of Arduino Nano
#define CHANNEL_UNDEFINED           -1
#define PWM_MAX                    255  // max value of 8bit pwm output
#define DISPLAY_STEP                25  // 1/10 * PWM_MAX
#define QUOTIENT_BETWEEN_8_AND_12_BIT_RESOLUTION         16
#define HALF_OF_QUOTIENT_BETWEEN_8_AND_12_BIT_RESOLUTION  8
#define UPDATE_CHANNEL_INDEPENDENTLY -1

const char pwmChannelMap[PWM_CHANNEL_COUNT] = {
  PWM_OUTPUT_CH0,
  PWM_OUTPUT_CH1,
  PWM_OUTPUT_CH2,
  PWM_OUTPUT_CH3,
  PWM_OUTPUT_CH4,
  PWM_OUTPUT_CH5
};

unsigned char outputs[PWM_CHANNEL_COUNT];     // Array for storing values of pwm channels

String inputBuffer = "";                      // Variable for storing received data


/*
 *  Outputs can be linked to an other channel.
 *  It means the linked new value of a linked channel will be setted on output
 *  only when the other channel (where it is linked) gets a new value.
 *  -1 means that channel is not linked anywhere.
 */
char outputBindings[PWM_CHANNEL_COUNT] = {
	UPDATE_CHANNEL_INDEPENDENTLY,
	UPDATE_CHANNEL_INDEPENDENTLY,
	UPDATE_CHANNEL_INDEPENDENTLY,
	UPDATE_CHANNEL_INDEPENDENTLY,
	UPDATE_CHANNEL_INDEPENDENTLY,
	UPDATE_CHANNEL_INDEPENDENTLY
};

void linkChannel(unsigned char what, unsigned char where){
	if( (what >= PWM_CHANNEL_COUNT) || (where >= PWM_CHANNEL_COUNT) || (what == where)){
		// We can link only the "own" channels together.
		// And we can NOT link a channel for himself.
		return;
	}
	outputBindings[what] = where;
}

//=================================================================================

void setup() {

  // sets the pin for PWM outputs
  pinMode(PWM_OUTPUT_CH0, OUTPUT);   
  pinMode(PWM_OUTPUT_CH1, OUTPUT);   
  pinMode(PWM_OUTPUT_CH2, OUTPUT);   
  pinMode(PWM_OUTPUT_CH3, OUTPUT);   
  pinMode(PWM_OUTPUT_CH4, OUTPUT);   
  pinMode(PWM_OUTPUT_CH5, OUTPUT);   
  
  // Set RGB channels together
  // Set output of ch0 and ch1 only when ch3 is updated.
  linkChannel(0, 2);
  linkChannel(1, 2);


  #ifdef USE_OLED_DISPLAY_I2C
    oled.begin(&Adafruit128x64, I2C_ADDRESS_OF_DISPLAY, true);
  #endif
  #ifdef USE_OLED_DISPLAY_SPI
    oled.begin(&Adafruit128x64, OLED_CS, OLED_DC, OLED_D0, OLED_D1, OLED_RST);
  #endif
  #if defined(USE_OLED_DISPLAY_I2C) || defined(USE_OLED_DISPLAY_SPI)
    oled.setFont(Adafruit5x7);  
    oled.clear();  
  #endif


  Serial.begin(SERIAL_INPUT_BAUNDRATE);   //Sets the baud for serial data transmission      
  delay(300);
  #ifdef HANDLE_FURTHER_CHANNELS  
    serialOutput.begin(SERIAL_OUTPUT_BAUNDRATE);
    delay(100);
  #endif

  unsigned char wasValueStored = 0;
  for(char i=0; i<PWM_CHANNEL_COUNT; i++){
    //outputs[i] = DEFAULT_OUTPUT_VALUE;
    unsigned char value = EEPROM.read(i);
    EEPROM.write(i, 0);
    outputs[i] = value;
    if(value != 0){
      wasValueStored = 1;
    }
    analogWrite(pwmChannelMap[i], outputs[i]);
  }

  #if defined(USE_OLED_DISPLAY_I2C) || defined(USE_OLED_DISPLAY_SPI)
    // Show start message on display
    oled.set2X();
    //oled.println("Serial\nPWM Driver\n" + String(VERSION));
    oled.println("Serial\nPWM Driver");
    oled.set1X();
    oled.println(String(VERSION) + "\n");

    #ifdef USE_12BIT_INPUT_VALUES
      oled.println("Input mode: 12 bit");
    #else
      oled.println("Input mode: 8 bit");
    #endif
    #ifdef HANDLE_FURTHER_CHANNELS  
      oled.println("Serial out enabled");
    #endif
     
    /*
    int i=0;
    String bindings = "B:";
    for(i=0; i<PWM_CHANNEL_COUNT; i++){
    	if(outputBindings[i] != UPDATE_CHANNEL_INDEPENDENTLY){
	        bindings += (" " + String(i) + "->" + String(outputBindings[i]) + ",");
        }
    }
    oled.println(bindings);

    /**/

  if(wasValueStored){
    showOutputs();
  }

  #endif

}

//=================================================================================

/*
 * Show the current values of own pwm channels on oled display. 
 *
 * Example output:
 *     "ch0:   7 #          "
 *     "ch1: 255 ###########"
 *     "ch2: 127 ######     "
 *     "ch3:   0            "
 *     "ch4:  40 ##         "
 *     "ch5:   0            "
 *
 * Note: this function will be compiled only if 
 *       USE_OLED_DISPLAY_I2C macro or USE_OLED_DISPLAY_SPI macro is used.
 *
 */
#if defined(USE_OLED_DISPLAY_I2C) || defined(USE_OLED_DISPLAY_SPI)
void showOutputs(){
  oled.clear();
  for(int ch=0; ch<PWM_CHANNEL_COUNT; ch++){
    byte barLength = (outputs[ch] / DISPLAY_STEP);
    String bar = " ";
    for(byte i=0; i<barLength; i++){
      bar += "#";
    }
    if((outputs[ch] > 0) && (barLength == 0)){
      bar += "#";
    }
    oled.println("ch" + String(ch) + ": " + (outputs[ch]<100?" ":"") + (outputs[ch]<10?" ":"") + outputs[ch] + bar);
  }
}
#endif


/*
 * Calculate the appropriate output value 
 * In case of "12bit mode", it calculatates the appropriate value for 8bit wide outputs.
 */
int calculateOutputValue(int input){
  int output;

  #ifdef USE_12BIT_INPUT_VALUES
    output = ((input + HALF_OF_QUOTIENT_BETWEEN_8_AND_12_BIT_RESOLUTION) / QUOTIENT_BETWEEN_8_AND_12_BIT_RESOLUTION);
  #else
    output = input;
  #endif

  // Keep output value in valide range [0..PWM_MAX]
  if(output > PWM_MAX) {
    output = PWM_MAX;
  }else
  if(output < 0) {
    output = 0;
  }

  return output;
}


/*
 * Create line to forward command that wants to set channel for a channel what is out of our range.
 * Calculates new channel id for forwarded command.
 *
 * Example input:
 *     inputChannelId:   8
 *     value:          255
 * Example output:
 *     "2 255"
 *
 * Overall channel 8 means the 2nd channel what is over our range,
 * so the 2nd channel of slave device is the 8th channel in overall.
 *
 * Note: this function will be compiled only if HANDLE_FURTHER_CHANNELS macro is used.
 *
 */
#ifdef HANDLE_FURTHER_CHANNELS
String buildCommandOutput(int inputChannelId, unsigned short value){
  unsigned short shiftedChannelId = inputChannelId - PWM_CHANNEL_COUNT;
  return (String(shiftedChannelId) + " " + String(value));
}
#endif


/*
 * Process input command (what received over serial port)
 * Sample inputs:
 *     - in  8bit mode: "2 255" -> 100% duty cycle of pwm output on channel 2
 *     - in 12bit mode: "0 2047" -> 50% duty cycle of pwm output on channel 0
 * This function does:
 *     - Gets the appropriate output value (in case of "12bit mode", it calculatates the appropriate value for 8bit wide outputs)
 *     - If channelId is within range of "own channels" (0..5) than it sets pwm outputs on specified channel.
 *     - If "HANDLE_FURTHER_CHANNELS" function enabled and the given channelId is out of "own channels" range 
 *       than it forwards the received command with decreased channel id for the "slave" instance.
 *     - If "using oled display" function is enabled then the current values of own channels will be shown on the display
 * 
 */
void processLine(String line){

  //int channel = ((String)(line.charAt(0))).toInt();
  int channel = ((String)(line.substring(0,line.indexOf(' ')))).toInt();
  if((channel < 0) 
      #ifndef HANDLE_FURTHER_CHANNELS
        || (channel >= PWM_CHANNEL_COUNT)
      #endif
  ){
    channel = CHANNEL_UNDEFINED;
  }

  if(channel > CHANNEL_UNDEFINED){
    int value = calculateOutputValue(((String)(line.substring(2))).toInt());
  
    if(channel < PWM_CHANNEL_COUNT){
      outputs[channel] = value;

      // Store current values
      EEPROM.write(channel, value); 
      //if(EEPROM.read(ADDR_COLOR_IS_STORED) == COLOR_IS_STORED){}

      if(outputBindings[channel] == UPDATE_CHANNEL_INDEPENDENTLY){
      
        // Set own pwm output of according to processed channel number and value..
        int i=0;
        for(; i<PWM_CHANNEL_COUNT; i++){
        	if(outputBindings[i] == channel){
        		// channel[i] has been binded to currently updated channel
        		analogWrite(pwmChannelMap[i], outputs[i]);
        	}
        }
        analogWrite(pwmChannelMap[channel], value);

        #if defined(USE_OLED_DISPLAY_I2C) || defined(USE_OLED_DISPLAY_SPI)
          showOutputs();
        #endif
      
      }else{
      	// Output channel has been binded to an other..

      	// Wanted output value is stored in outputs[] so..
      	// Do nothing now..
      }
    }
    #ifdef HANDLE_FURTHER_CHANNELS
      else{ 
        // Forward commands of futher channels for the other device over softSerial bus
        serialOutput.print( buildCommandOutput(channel, value) + "\n" );
      }
    #endif

  }

}



void loop(){

  while (Serial.available()) {
    delay(3);  //delay to allow buffer to fill 
    if (Serial.available() > 0) {
      char c = Serial.read();  //gets one byte from serial buffer
      if(c != '\n'){
        inputBuffer += c; //build an inputBuffer string from received charachters
      }else{
        processLine(inputBuffer);
        inputBuffer = "";
      }
    } 
  }

}

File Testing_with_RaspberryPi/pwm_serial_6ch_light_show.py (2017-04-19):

from __future__ import division
import time
import argparse
import os
import datetime
import serial

# Constants
output_channel_of_green = 2 	# 0
output_channel_of_blue  = 0
output_channel_of_red   = 1

output_channel_of_red2   = 3
output_channel_of_green2 = 4
output_channel_of_blue2  = 5

def write_to_file(data):
	homePath = os.environ["HOME"]
	with open(homePath + "/logs/rgb_output.log", "a") as myfile:
		myfile.write(data + "\r\n")
		myfile.close()

# Uncomment to enable debug output.
#import logging
#logging.basicConfig(level=logging.DEBUG)

# Initialise the serial output.
ser = serial.Serial(
   port='/dev/ttyAMA0',
   baudrate = 9600,
   parity=serial.PARITY_NONE,
   stopbits=serial.STOPBITS_ONE,
   bytesize=serial.EIGHTBITS,
   timeout=1
)

def sendOutputCommandOnSerial(command):
	ser.write(command + "\n");

# Parse arguments
parser = argparse.ArgumentParser('RGB test')
parser.add_argument("-r","--red", type=int, help="red", default = -1)
parser.add_argument("-g","--green", type=int, help="green", default = -1)
parser.add_argument("-b","--blue", type=int, help="blue", default = -1)

parser.add_argument("-x", "--hex", type=str, help="RGB color in hex string", default = "  ")
parser.add_argument("-c", "--complete", type=str, help="all color component in one", default = "  ")

parser.add_argument("-ch3","--ch3", type=int, help="channel_3", default = 0)
parser.add_argument("-ch4","--ch4", type=int, help="channel_4", default = 0)
parser.add_argument("-ch5","--ch5", type=int, help="channel_5", default = 0)

args = parser.parse_args()

allComponent = args.complete

# Store values for each color-channel
red1   = args.red
green1 = args.green
blue1  = args.blue

red2 = args.ch3
green2 = args.ch4
blue2 = args.ch5


# Set PWM outputs
direction = 1
while True:

	if direction:

		for i in xrange(16,2047):
			r1 = int((red1*i/4096) * i)
			g1 = int((green1*1/4096) * i)
			b1 = int((blue1*1/4096) * i)
			r2 = (red2 * (2048-i)/4096)
			g2 = (green2 * (2048-i)/4096)
			b2 = (blue2 * (2048-i)/4096)
			sendOutputCommandOnSerial(str(output_channel_of_blue)  + " " + str(b1));
			sendOutputCommandOnSerial(str(output_channel_of_red)   + " " + str(r1));
			sendOutputCommandOnSerial(str(output_channel_of_green) + " " + str(g1));
			sendOutputCommandOnSerial("3 " + str(r2));
			sendOutputCommandOnSerial("4 " + str(g2));
			sendOutputCommandOnSerial("5 " + str(b2));

		for i in xrange(2047,16):
			r1 = int((red1*i/4096) * i)
			g1 = int((green1*1/4096) * i)
			b1 = int((blue1*1/4096) * i)
			r2 = (red2 * (2048-i)/4096)
			g2 = (green2 * (2048-i)/4096)
			b2 = (blue2 * (2048-i)/4096)
			sendOutputCommandOnSerial(str(output_channel_of_blue)  + " " + str(b1));
			sendOutputCommandOnSerial(str(output_channel_of_red)   + " " + str(r1));
			sendOutputCommandOnSerial(str(output_channel_of_green) + " " + str(g1));
			sendOutputCommandOnSerial("3 " + str(r2));
			sendOutputCommandOnSerial("4 " + str(g2));
			sendOutputCommandOnSerial("5 " + str(b2));


# Write log
#lasttime = str(datetime.datetime.time(datetime.datetime.now()))[:8]
#write_to_file(lasttime + "\tR:" + str(red) + "\tG: " + str(green) + "\tB: " + str(blue) )
    

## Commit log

2017-01-26 Add schematic for testing v1.0
    [Schematic.fzz]
2017-01-26 Add testcode for send pwm commands in serial bus from RaspberryPi
2017-01-27 Add option for use Oled display over SPI protocol
2017-01-28 Add feature for handle 8 or 12 bit pwm commands too
2017-01-28 Move schematic(s) to separated folder
    [BreadBoard_test_schematic.fzz]
2017-01-29 Eagle schematic added
    [PCB_schematic_v1.0.sch]
2017-01-29 Eagle design will be stored as .zip
    [BreadBoard_test_schematic.fzz, PCB_schematic_v1.0.sch]
2017-01-29 Eagle pcb desin added
2017-01-29 Add Eagle PCB design
2017-01-29 Add datasheet for used FET
2017-01-29 Add partlist for PCB with I2C output version
2017-01-29 PCB design changed to leave place for attach I2C oled display
2017-01-30 Add partlist as xls
    [PCB_schematic_v1.0_I2C_part-list.xlsx]
2017-01-31 Minor changes after 1st test without second device
2017-01-31 Add serial-output on PCB design
2017-01-31 Add image of breadBoard sample
2017-02-04 Further channel bug fixed
    [Serial_PWM_Driver_with_OLED.ino]
2017-02-04 Change pin order of SPI display accoridng to pin order on display's pcb
2017-02-06 Add ready for test version of schematic design
    [Output_test_schematic.fzz]
2017-02-08 Add download link for PCB design PDF
2017-02-22 PCB 1.42 - Add VCC in terminal and header
2017-02-22 PCB 1.42
2017-02-22 Add pcb design v1.42
2017-02-22 update pcb pdf links
2017-02-22 update pcb pdf link
2017-02-25 Add overall part testing images and update pcb design
2017-02-25 Update schematic and pcb v1.44
2017-02-25 Add pcb design v1.44 as pdf
2017-02-25 Update readme after overall testing with pcb design 1.44
2017-03-14 Add pdf-s to pcb creation of v1.44
2017-03-16 Add printable PCB designs
2017-03-17 Add softSerial out; Create RTM pcb design (1.45)
2017-03-17 Update PCB bottom view for direct print
2017-03-17 Update printable PDF
2017-03-18 Add printed version
2017-03-18 Update pcb design image
2017-03-20 Add partlist for buy
    [partlist.xlsx, partlist_buy.xlsx]
2017-03-20 Update buy-list
    [partlist_buy.xlsx]
2017-03-21 Move part-lists to appropirate folder
    [PCB_schematic_v1.0_I2C_part-list.xlsx, partlist.xlsx, partlist_buy.xlsx]
2017-03-22 Add photos of PCB breadboard and first dry test
2017-03-22 Update readme after prototype dry test
2017-03-22 Change order of output channels according to RGB led strip
2017-03-23 Add fritzling schematic only for a sample of connection with raspberry pi
    [Connected_to_RaspberryPiZero.fzz]
2017-03-23 Add description for connection between the board and a raspberryPi
2017-03-24 Issues with using serial from python on other raspberry
2017-03-25 Change output binding for use with Pi-Tasker
    [Serial_PWM_Driver_with_OLED.ino]
2017-04-19 Beta test phase done. Dismount display from PWM driver
